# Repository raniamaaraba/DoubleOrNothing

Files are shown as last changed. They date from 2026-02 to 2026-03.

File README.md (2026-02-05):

# PCB Development in KiCAD
For this semester, we will be creating custom PCBs (printed circuit boards) in a free software called [KiCAD](https://www.kicad.org/download/), primarily for the use of condensing space inside the avionics bay and to move the club further towards the goal of a space shot in which custom PCBs would be critical to the development of avionics. Before we decide on a final design, in order to easily share and access the schematics, we will be using GitHub as a form of version control. Notably, before we get into the actual logistics of GitHub itself, I wanted to create a comprehensive list _(as of 2/5/26)_ of the parts that we will be using

| Coloquial Name  | Name |
| --- | --- |
| Microcontroller  | ESP32-S3  |
| Battery | LiPO  |
| Barometer | MS561101BA03-50 |
| IMU | LSM6DSO32TR |
| MOSFET| TBD |
| Resistor| Generic for now |
| Capacitor | Also Generic |

There should be a ZIP file included to help for some of the imports, if you cannot find a specific item you are looking for, please reach out to Loring. Also note the current PCBs on the main branch of KiCAD are primarily for demonstration and by no means are the current version of what we are making. 

# Forking and GitHub
Since I am the owner of this repository, I cannot demonstrate how to fork a repository but I can link you to the GitHub Page about this--click [here](https://docs.github.com/en/pull-requests/collaborating-with-pull-requests/working-with-forks/fork-a-repo) to read how before adding your own commits. This ensure that everyone can keep version control of their PCB without effecting the current main PCB. If you have any issues with Forking this repository (make sure it is the KiCAD branch), please reach out! Also want to note unlike when it come to coding development, it is significantly easier to manage uploading files and pushes using the online GitHub website rather than the desktop.

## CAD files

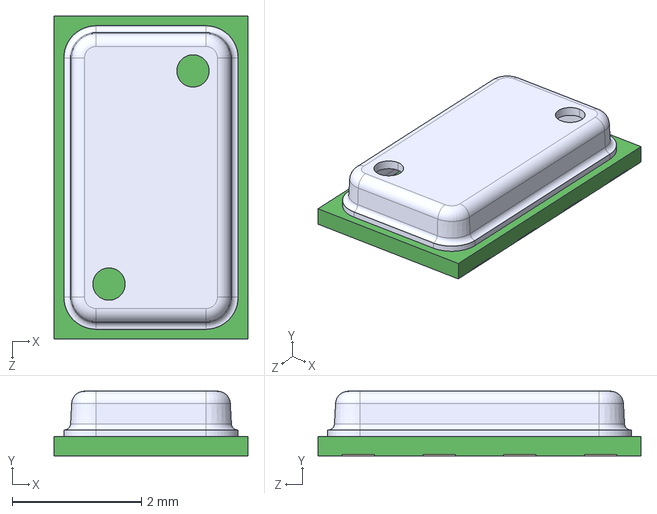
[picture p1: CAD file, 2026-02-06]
3D models/MS561101BA03-50--3DModel-STEP-56544.STEP
3.00 x 1.00 x 5.00 mm

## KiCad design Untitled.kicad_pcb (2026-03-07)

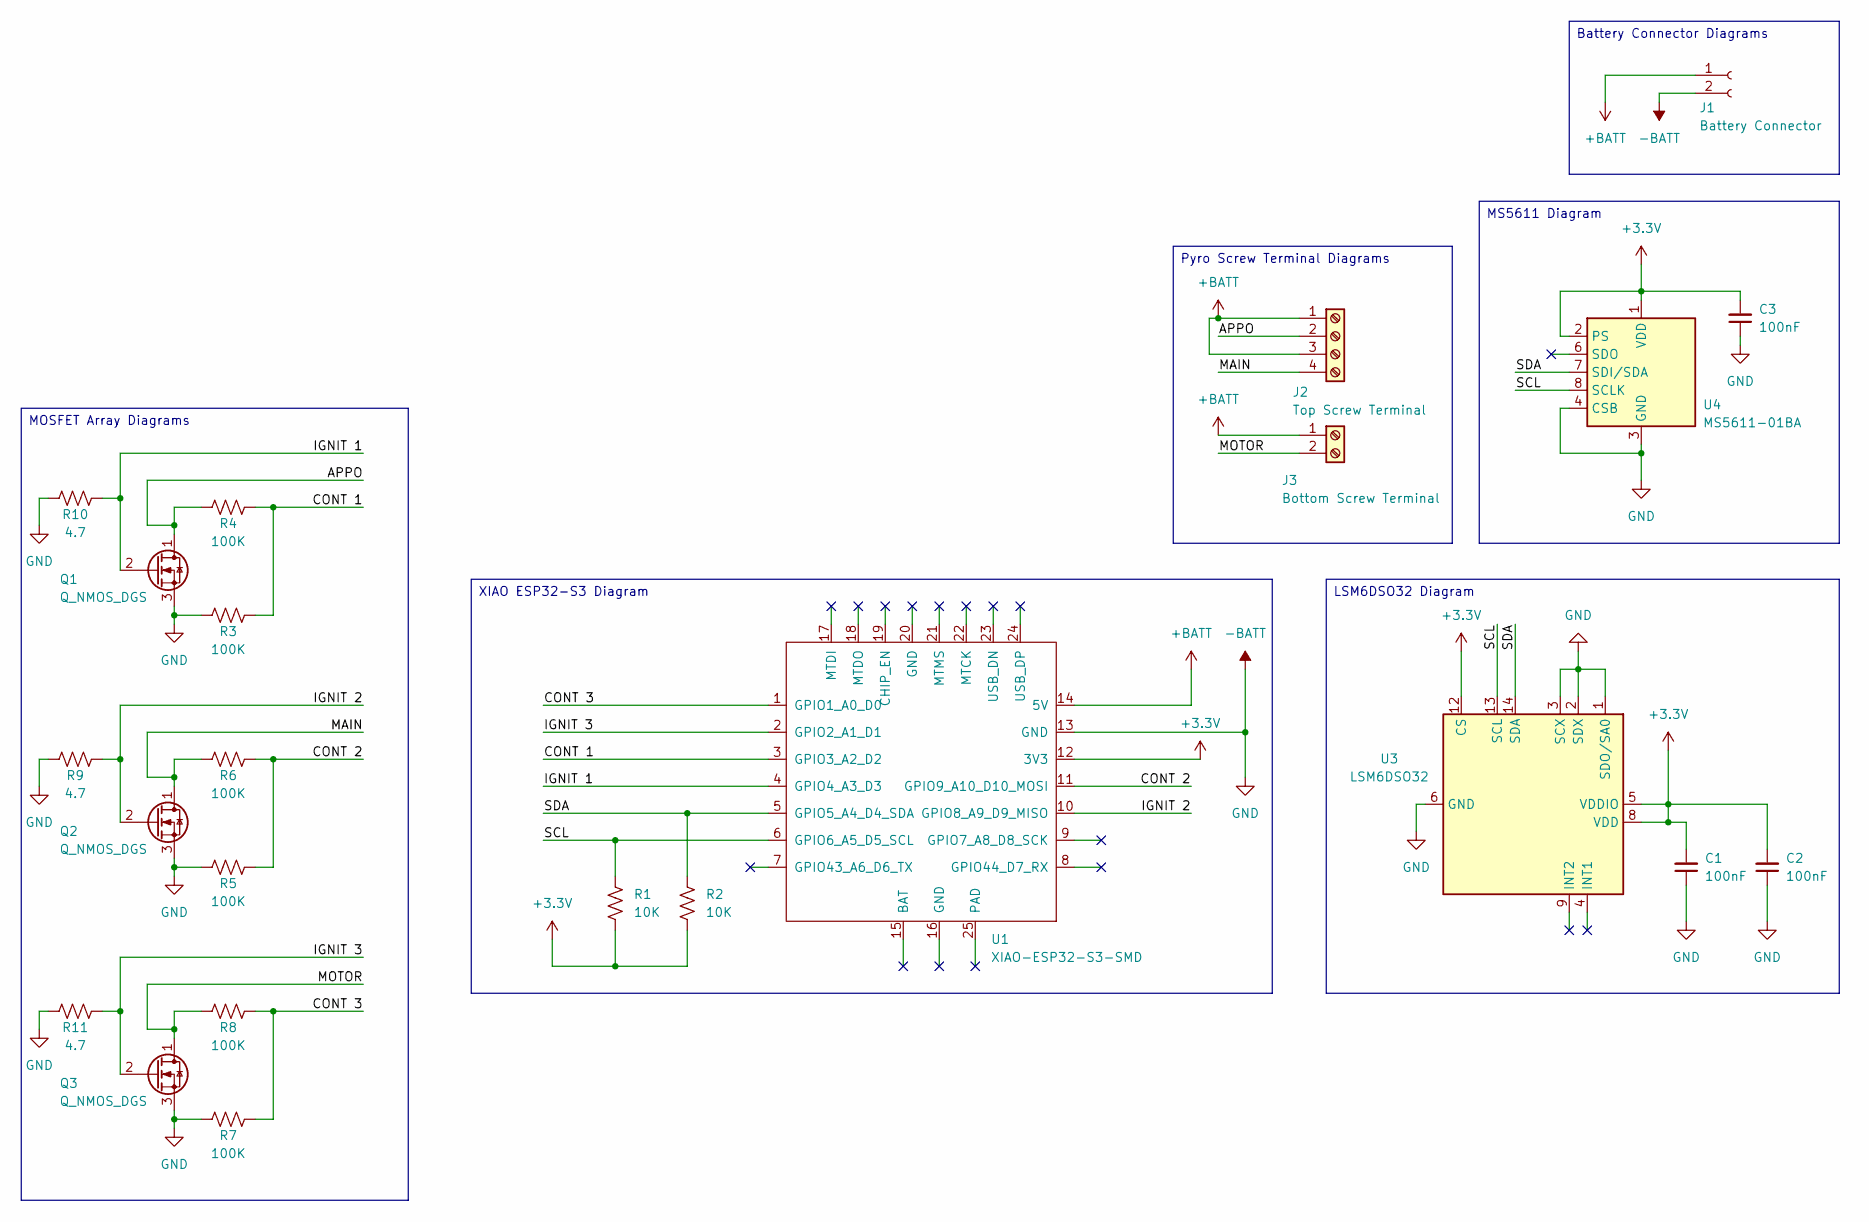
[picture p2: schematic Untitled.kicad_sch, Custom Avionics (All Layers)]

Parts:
C1, C2, C3: 100nF; C_0603_1608Metric
J1: Battery Connector; JST_PH_B2B-PH-K_1x02_P2.00mm_Vertical
J2: Top Screw Terminal; TerminalBlock_Phoenix_MPT-0,5-4-2.54_1x04_P2.54mm_Horizontal
J3: Bottom Screw Terminal; TerminalBlock_Phoenix_MPT-0,5-2-2.54_1x02_P2.54mm_Horizontal
Q1, Q2, Q3: Q_NMOS_DGS; TSOT-23
R1, R2: 10K; R_0402_1005Metric
R3, R4, R5, R6, R7, R8: 100K; R_0402_1005Metric
R9, R10, R11: 4.7; R_0402_1005Metric
U1: XIAO-ESP32-S3-SMD; XIAO-ESP32S3-DIP
U3: LSM6DSO32; LGA-14_3x2.5mm_P0.5mm_LayoutBorder3x4y
U4: MS5611-01BA; LGA-8_3x5mm_P1.25mm

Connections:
+3.3V: C1.2, C2.2, C3.2, R1.2, R2.2, U1.12 (3V3), U3.5 (VDDIO), U3.8 (VDD), U3.12 (CS), U4.1 (VDD), U4.2 (PS)
+BATT: J1.1, J2.1, J2.3, J3.1, U1.14 (5V)
-BATT: C1.1, C2.1, C3.1, J1.2, Q1.3 (S), Q2.3 (S), Q3.3 (S), R3.2, R5.2, R7.2, R9.2, R10.2, R11.2, U1.13 (GND), U3.1 (SDO/SA0), U3.2 (SDX), U3.3 (SCX), U3.6 (GND), U3.7 (GND), U4.3 (GND), U4.4 (CSB), U4.5 (CSB)
/APPO: J2.2, Q1.1 (D), R4.2
/CONT 1: R3.1, R4.1, U1.3 (GPIO3_A2_D2)
/CONT 2: R5.1, R6.1, U1.11 (GPIO9_A10_D10_MOSI)
/CONT 3: R7.1, R8.1, U1.1 (GPIO1_A0_D0)
/IGNIT 1: Q1.2 (G), R10.1, U1.4 (GPIO4_A3_D3)
/IGNIT 2: Q2.2 (G), R9.1, U1.10 (GPIO8_A9_D9_MISO)
/IGNIT 3: Q3.2 (G), R11.1, U1.2 (GPIO2_A1_D1)
/MAIN: J2.4, Q2.1 (D), R6.2
/MOTOR: J3.2, Q3.1 (D), R8.2
/SCL: R1.1, U1.6 (GPIO6_A5_D5_SCL), U3.13 (SCL), U4.8 (SCLK)
/SDA: R2.1, U1.5 (GPIO5_A4_D4_SDA), U3.14 (SDA), U4.7 (SDI/SDA)

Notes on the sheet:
XIAO ESP32-S3 Diagram
LSM6DSO32 Diagram
MS5611 Diagram
Battery Connector Diagrams
MOSFET Array Diagrams
Pyro Screw Terminal Diagrams

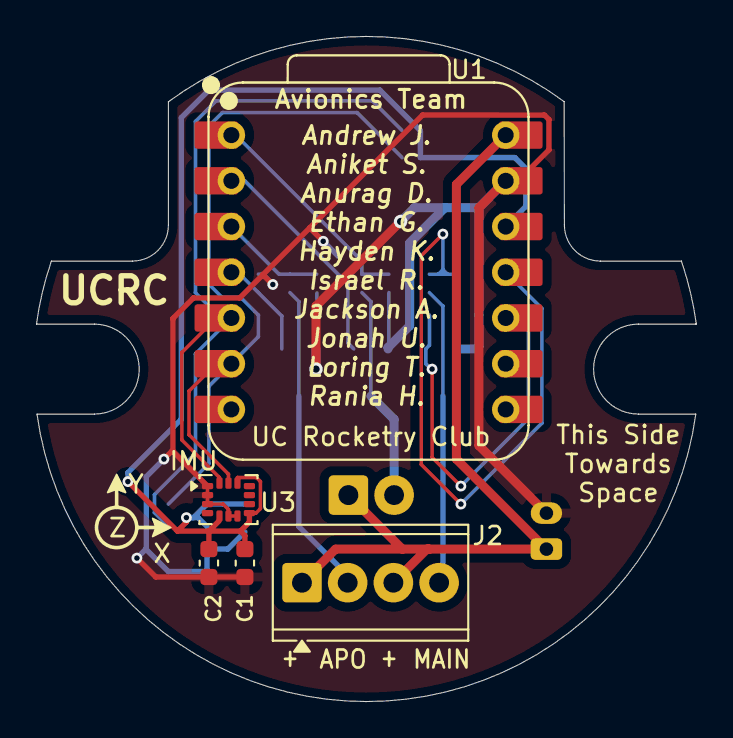
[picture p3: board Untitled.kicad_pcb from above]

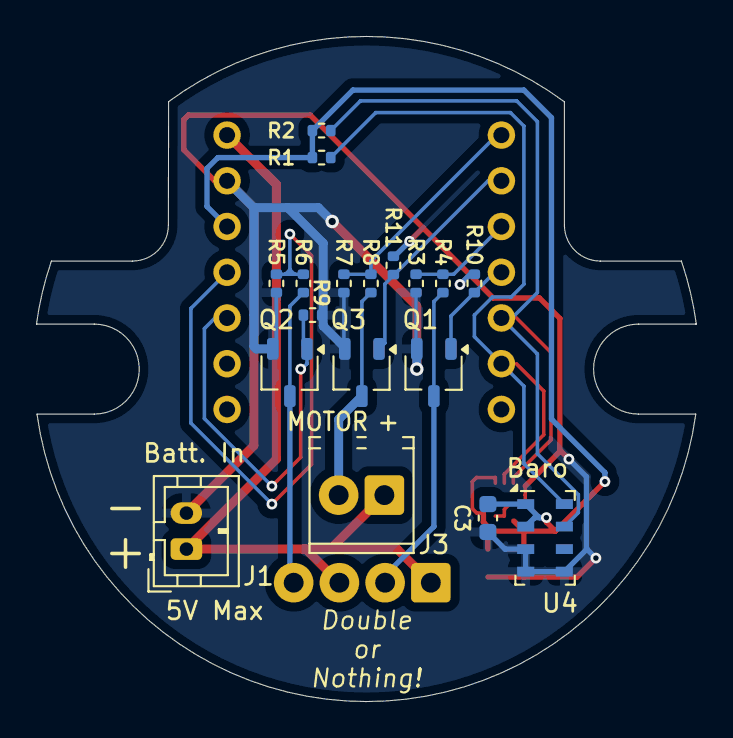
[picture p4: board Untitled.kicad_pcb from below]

Board: 2 copper layers, 36.7 x 37.0 mm, 23 parts (18 on the bottom side), 14 nets.

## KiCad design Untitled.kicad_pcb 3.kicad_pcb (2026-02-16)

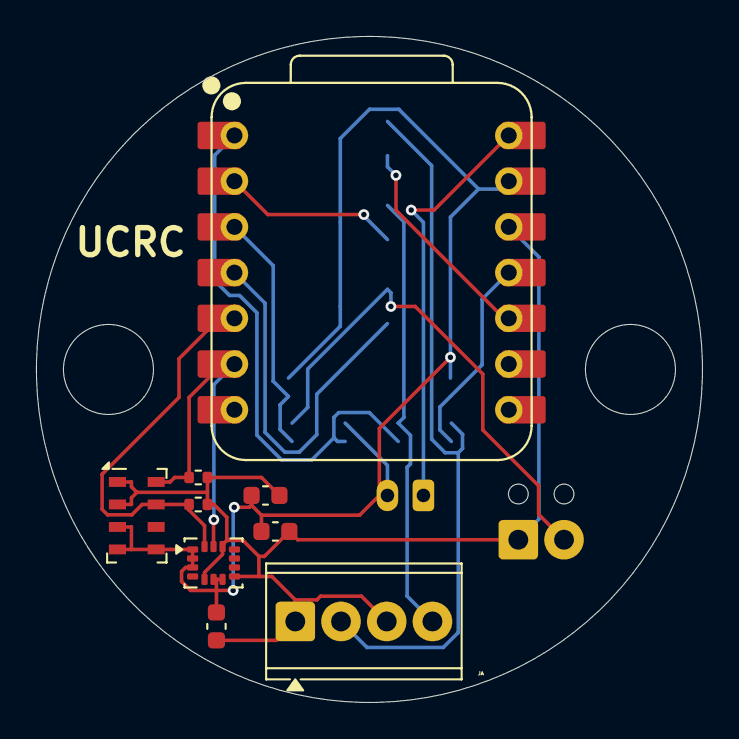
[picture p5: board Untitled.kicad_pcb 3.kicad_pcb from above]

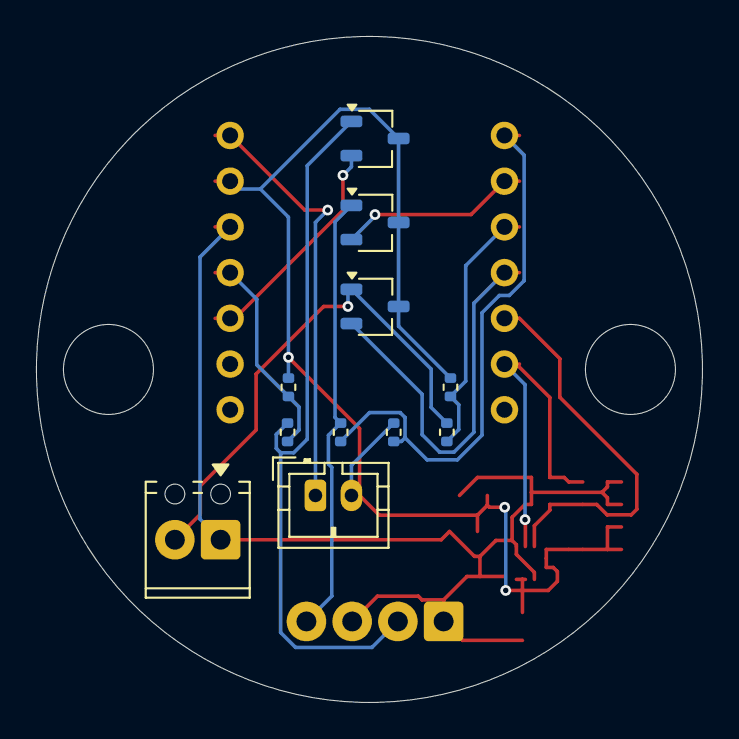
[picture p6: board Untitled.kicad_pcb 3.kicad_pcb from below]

Board: 2 copper layers, 37.0 x 37.0 mm, 21 parts (11 on the bottom side), 14 nets.

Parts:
C1, C2, C3: 100nF; C_0603_1608Metric
J1: Battery Connector; JST_PH_B2B-PH-K_1x02_P2.00mm_Vertical
J2: Top Screw Terminal; TerminalBlock_Phoenix_MPT-0,5-4-2.54_1x04_P2.54mm_Horizontal
J3: Bottom Screw Terminal; TerminalBlock_Phoenix_MPT-0,5-2-2.54_1x02_P2.54mm_Horizontal
Q1, Q2, Q3: Q_NMOS_DGS; TSOT-23
R1, R2, R3, R4, R5, R6, R7, R8: 10K; R_0402_1005Metric
Trust: MountingHole_5mm
U1: XIAO-ESP32-S3-SMD; XIAO-ESP32S3-DIP
U3: LSM6DSO32; LGA-14_3x2.5mm_P0.5mm_LayoutBorder3x4y
U4: MS5611-01BA; LGA-8_3x5mm_P1.25mm

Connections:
+3.3V: C1.2, C2.2, C3.2, J2.1, J2.3, J3.1, R1.2, R2.2, U1.12 (3V3), U3.5 (VDDIO), U3.8 (VDD), U3.12 (CS), U4.1 (VDD), U4.2 (PS)
+BATT: J1.1, U1.14 (5V)
-BATT: C1.1, C2.1, C3.1, J1.2, Q1.3 (S), Q2.3 (S), Q3.3 (S), R3.2, R6.2, R8.2, U1.13 (GND), U3.1 (SDO/SA0), U3.2 (SDX), U3.3 (SCX), U3.6 (GND), U3.7 (GND), U4.3 (GND), U4.4 (CSB), U4.5 (CSB)
/APPO: J2.2, Q1.1 (D), R4.2
/CONT 1: R3.1, R4.1, U1.11 (GPIO9_A10_D10_MOSI)
/CONT 2: R5.1, R6.1, U1.1 (GPIO1_A0_D0)
/CONT 3: R7.1, R8.1, U1.3 (GPIO3_A2_D2)
/IGNIT 1: Q1.2 (G), U1.10 (GPIO8_A9_D9_MISO)
/IGNIT 2: Q2.2 (G), U1.2 (GPIO2_A1_D1)
/IGNIT 3: Q3.2 (G), U1.4 (GPIO4_A3_D3)
/MAIN: J2.4, Q2.1 (D), R5.2
/MOTOR: J3.2, Q3.1 (D), R7.2
/SCL: R1.1, U1.6 (GPIO6_A5_D5_SCL), U3.13 (SCL), U4.8 (SCLK)
/SDA: R2.1, U1.5 (GPIO5_A4_D4_SDA), U3.14 (SDA), U4.7 (SDI/SDA)

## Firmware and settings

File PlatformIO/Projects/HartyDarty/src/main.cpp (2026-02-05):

#include <Arduino.h>
#include <Adafruit_LSM6DSO32.h>
// put function declarations here:
int myFunction(int, int);

void setup() {
  // put your setup code here, to run once:
  int result = myFunction(2, 3);
}

void loop() {
  // put your main code here, to run repeatedly:
}
// hehe nerds --> Jesse is best coder >:)
// put function definitions here:
int myFunction(int x, int y) {
  return x + y;
}



// Basic demo for accelerometer & gyro readings from Adafruit
// LSM6DSO32 sensor
#include <Adafruit_LSM6DSO32.h>
// For SPI mode, we need a CS pin
#define LSM_CS 10
// For software-SPI mode we need SCK/MOSI/MISO pins
#define LSM_SCK 13
#define LSM_MISO 12
#define LSM_MOSI 11

Adafruit_LSM6DSO32 dso32;
void setup(void) {
  Serial.begin(115200);
  while (!Serial)
    delay(10); // will pause Zero, Leonardo, etc until serial console opens

  Serial.println("Adafruit LSM6DSO32 test!");

  if (!dso32.begin_I2C()) {
    // if (!dso32.begin_SPI(LSM_CS)) {
    // if (!dso32.begin_SPI(LSM_CS, LSM_SCK, LSM_MISO, LSM_MOSI)) {
    // Serial.println("Failed to find LSM6DSO32 chip");
    while (1) {
      delay(10);
    }
  }

  Serial.println("LSM6DSO32 Found!");

  dso32.setAccelRange(LSM6DSO32_ACCEL_RANGE_8_G);
  Serial.print("Accelerometer range set to: ");
  switch (dso32.getAccelRange()) {
  case LSM6DSO32_ACCEL_RANGE_4_G:
    Serial.println("+-4G");
    break;
  case LSM6DSO32_ACCEL_RANGE_8_G:
    Serial.println("+-8G");
    break;
  case LSM6DSO32_ACCEL_RANGE_16_G:
    Serial.println("+-16G");
    break;
  case LSM6DSO32_ACCEL_RANGE_32_G:
    Serial.println("+-32G");
    break;
  }

  // dso32.setGyroRange(LSM6DS_GYRO_RANGE_250_DPS );
  Serial.print("Gyro range set to: ");
  switch (dso32.getGyroRange()) {
  case LSM6DS_GYRO_RANGE_125_DPS:
    Serial.println("125 degrees/s");
    break;
  case LSM6DS_GYRO_RANGE_250_DPS:
    Serial.println("250 degrees/s");
    break;
  case LSM6DS_GYRO_RANGE_500_DPS:
    Serial.println("500 degrees/s");
    break;
  case LSM6DS_GYRO_RANGE_1000_DPS:
    Serial.println("1000 degrees/s");
    break;
  case LSM6DS_GYRO_RANGE_2000_DPS:
    Serial.println("2000 degrees/s");
    break;
  case ISM330DHCX_GYRO_RANGE_4000_DPS:
    break; // unsupported range for the DSO32
  }

  // dso32.setAccelDataRate(LSM6DS_RATE_12_5_HZ);
  Serial.print("Accelerometer data rate set to: ");
  switch (dso32.getAccelDataRate()) {
  case LSM6DS_RATE_SHUTDOWN:
    Serial.println("0 Hz");
    break;
  case LSM6DS_RATE_12_5_HZ:
    Serial.println("12.5 Hz");
    break;
  case LSM6DS_RATE_26_HZ:
    Serial.println("26 Hz");
    break;
  case LSM6DS_RATE_52_HZ:
    Serial.println("52 Hz");
    break;
  case LSM6DS_RATE_104_HZ:
    Serial.println("104 Hz");
    break;
  case LSM6DS_RATE_208_HZ:
    Serial.println("208 Hz");
    break;
  case LSM6DS_RATE_416_HZ:
    Serial.println("416 Hz");
    break;
  case LSM6DS_RATE_833_HZ:
    Serial.println("833 Hz");
    break;
  case LSM6DS_RATE_1_66K_HZ:
    Serial.println("1.66 KHz");
    break;
  case LSM6DS_RATE_3_33K_HZ:
    Serial.println("3.33 KHz");
    break;
  case LSM6DS_RATE_6_66K_HZ:
    Serial.println("6.66 KHz");
    break;
  }

  // dso32.setGyroDataRate(LSM6DS_RATE_12_5_HZ);
  Serial.print("Gyro data rate set to: ");
  switch (dso32.getGyroDataRate()) {
  case LSM6DS_RATE_SHUTDOWN:
    Serial.println("0 Hz");
    break;
  case LSM6DS_RATE_12_5_HZ:
    Serial.println("12.5 Hz");
    break;
  case LSM6DS_RATE_26_HZ:
    Serial.println("26 Hz");
    break;
  case LSM6DS_RATE_52_HZ:
    Serial.println("52 Hz");
    break;
  case LSM6DS_RATE_104_HZ:
    Serial.println("104 Hz");
    break;
  case LSM6DS_RATE_208_HZ:
    Serial.println("208 Hz");
    break;
  case LSM6DS_RATE_416_HZ:
    Serial.println("416 Hz");
    break;
  case LSM6DS_RATE_833_HZ:
    Serial.println("833 Hz");
    break;
  case LSM6DS_RATE_1_66K_HZ:
    Serial.println("1.66 KHz");
    break;
  case LSM6DS_RATE_3_33K_HZ:
    Serial.println("3.33 KHz");
    break;
  case LSM6DS_RATE_6_66K_HZ:
    Serial.println("6.66 KHz");
    break;
  }
}

void loop() {

  //  /* Get a new normalized sensor event */
  sensors_event_t accel;
  sensors_event_t gyro;
  sensors_event_t temp;
  dso32.getEvent(&accel, &gyro, &temp);

  Serial.print("\t\tTemperature ");
  Serial.print(temp.temperature);
  Serial.println(" deg C");

  /* Display the results (acceleration is measured in m/s^2) */
  Serial.print("\t\tAccel X: ");
  Serial.print(accel.acceleration.x);
  Serial.print(" \tY: ");
  Serial.print(accel.acceleration.y);
  Serial.print(" \tZ: ");
  Serial.print(accel.acceleration.z);
  Serial.println(" m/s^2 ");

  /* Display the results (rotation is measured in rad/s) */
  Serial.print("\t\tGyro X: ");
  Serial.print(gyro.gyro.x);
  Serial.print(" \tY: ");
  Serial.print(gyro.gyro.y);
  Serial.print(" \tZ: ");
  Serial.print(gyro.gyro.z);
  Serial.println(" radians/s ");
  Serial.println();

  delay(100);

  //  // serial plotter friendly format

  //  Serial.print(temp.temperature);
  //  Serial.print(",");

  //  Serial.print(accel.acceleration.x);
  //  Serial.print(","); Serial.print(accel.acceleration.y);
  //  Serial.print(","); Serial.print(accel.acceleration.z);
  //  Serial.print(",");

  // Serial.print(gyro.gyro.x);
  // Serial.print(","); Serial.print(gyro.gyro.y);
  // Serial.print(","); Serial.print(gyro.gyro.z);
  // Serial.println();
  //  delayMicroseconds(10000);
}

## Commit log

2026-02-05 Revise README for PCB development in KiCAD
    Updated project title and added detailed PCB development information, including parts list and forking instructions.
2026-02-06 step files for 3d modeling
    [MS561101BA03-50--3DModel-STEP-56544.STEP]
2026-02-08 Added Correct Microcontroller
    Add the correct symbol for the microcontroller library
    [Untitled.kicad_sch]
2026-02-08 Fixed Microcontroller Library
    [Untitled.kicad_sch]
2026-02-08 Fixed Version Conflicts
    Fixed version issues, should now have all required files in correct versions for the KiCad to run
    [Untitled.kicad_pcb]
2026-02-10 Sensor Wiring Finished
    Finished the wiring for both sensors. Cleaned up diagram by using net labels rather than directly connecting everything. Left MOSTFETs unfinished bc they will likely be on a separate board.
    [Untitled.kicad_sch]
2026-02-10 Finished Schematic & Assigned Footprints
    Finished up the schematic, making this version applicable to the entire system rather than a single layer. Assigned footprints for every schematic component, did some very basic layout in the schemat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
    [Untitled.kicad_pcb, Untitled.kicad_sch]
2026-02-11 Experimental Layout
    Changed screw terminal footprint to accurately reflect existing club stock of smaller terminals (2.54mm pitch thru-hole). Experimented with trying to make a single board layout work for the flight co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
    [Untitled.kicad_pcb, Untitled.kicad_sch]
2026-02-12 Basic Schematic (NO PCB DESIGN DONE)
    Removed any PCB design so people can fork off and do their own PCB designs.
    [Untitled.kicad_pcb, Untitled.kicad_sch]
2026-02-16 My PCB design
    I arranged the parts and then used an automatic routing thingy to attach all of the nodes. I then made sure it followed the design rules checker and that's it.
    [Untitled.kicad 2_pcb.kicad_pcb, Untitled.kicad_pcb 3.kicad_pcb]
2026-02-17 I forgot to save the PCB file so it autosaved and that's alot of bloat
    Also the design I did is the untitled one, the numbered untitled ones are when i was doing something weird with saving copies but doing that doesn't link it to the schematic file.
    [Untitled.kicad_pcb]
2026-02-17 Added silkscreens
    Added the silkscreens that have the part numbers onto the PCB Schematic. From what I understand, the silkscreens can go overtop the copper tracks because they are on different layers. If that's not t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
    [Untitled.kicad_pcb]
2026-02-26 Changed Mosfet pad arrangement and Screwport terminal location
    Minor silksreen changes were also made.
    [Untitled.kicad_pcb]
2026-03-01 Added cutouts, spaced rod holes
    Added cutouts to the side of the PCB for wires to pass through on both sides of the ESP32. Changed distance between screw holes to accurately reflect the spacing used for threaded rods on previous av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
    [Untitled.kicad_pcb, Untitled.kicad_sch]
2026-03-01 Initial Routing
    Completed initial manual routing of PCB traces. All nets are fully connected.
    [Untitled.kicad_pcb, Untitled.kicad_sch]
2026-03-01 Silkscreen and Cleanup
    Added needed silkscreen elements like screw terminal labels and IMU axis indicator. Also added some UCRC related text and added (placeholder for now) avionics team member names below ESP32 cutout.
    [Untitled.kicad_pcb]
2026-03-01 Small Silkscreen Changes
    Added indicator for intended direction and made part label formatting consistent. Also added Jebediah Kerman to the list of fake names
    [Untitled.kicad_pcb]
2026-03-04 Small Changes
    Did some small changes to silkscreen formatting.
    [Untitled.kicad_pcb, Untitled.kicad_sch]
2026-03-05 Hole Updates and Initial Names
    Updated the threaded rod holes to extend to the PCB edge due to them previously leaving such a small gap near the sides of the holes. Drill footprints still there for now, will be removed in final ve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
    [Untitled.kicad_pcb, Untitled.kicad_sch]
2026-03-05 New Rgs Resistors and Ground Pour
    Added a set of 3 new resistors that bridge the gate of the MOSFETs to ground with a 4.7 ohm resistor, which can help filter out any unintentional activation of the MOSFET due to interference (detailed in datasheet). Also added a ground pour to the PCB for added EMI resistance and overall higher performance.
    [Untitled.kicad_pcb, Untitled.kicad_sch]
2026-03-05 Tiny Silkscreen Change
    Re-formatted the names silkscreen so that the names look more centered.
    [Untitled.kicad_pcb]
2026-03-05 Updated Names and Changed Formatting
    Added a 10th name to the list from the Microsoft Form. Adjusted spacing of several parts of the silkscreen under the ESP32: Separated the "Avionics Team" title from the names, made the names slightly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
    [Untitled.kicad_pcb]
2026-03-06 Small Changes
    Moved some trace routing to further prevent potential spacing conflicts.
    [Untitled.kicad_pcb]
2026-03-07 Initial Order Version
    Made small adjustments to via layout. Removed drill footprints for threaded rod holes from drawing.
    [Untitled-B_Cu.gbl, Untitled-B_Mask.gbs, Untitled-B_Paste.gbp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]
